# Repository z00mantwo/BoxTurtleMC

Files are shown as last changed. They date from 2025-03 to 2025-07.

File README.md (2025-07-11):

# BoxTurtleMC 
BoxTurtle Motor Controller. This is a self sourced DC motor controller for use with [Klipper](https://github.com/ArmoredTurtle/BoxTurtleg) and the  [BoxTurtle](https://klipper3d.org) project. This is not an official [Armored Turtle](https://github.com/ArmoredTurtle) project. Please read the entire file before ordering any parts so you know your options and what is involved. 

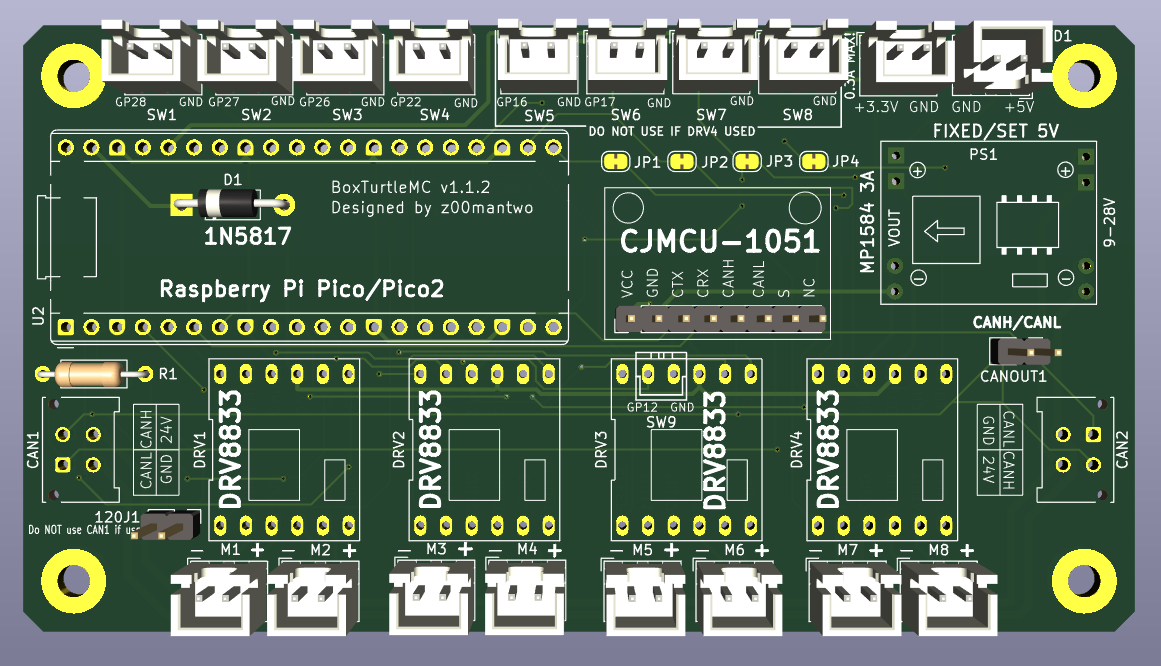
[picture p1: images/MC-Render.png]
BT_Render


The main focus is combining this project with a [BigTreeTech MMB](https://biqu.equipment/products/bigtreetech-mmb). This will enable full BoxTurtle control of the DC motor powered re-spoolers. It also allows a nice upgrade path from a ERCF to the BoxTurtle. It includes additional switch ports to support the "BoxTurtle Lane Controls" mod and additional power connections to support  [Project TurtleScreen](https://github.com/sbtoonz/TurtleScreen). This board will also have the option of controlling up to 8 re-spooler motors so it should be useful in larger custom BoxTurtle setups with more than 4 lanes. 

The board was developed in the free version of [KiCAD](https://www.kicad.org/). So it can be downloaded and modified.

Note there is a mount for the board in the stl folder.

## Making a PCB
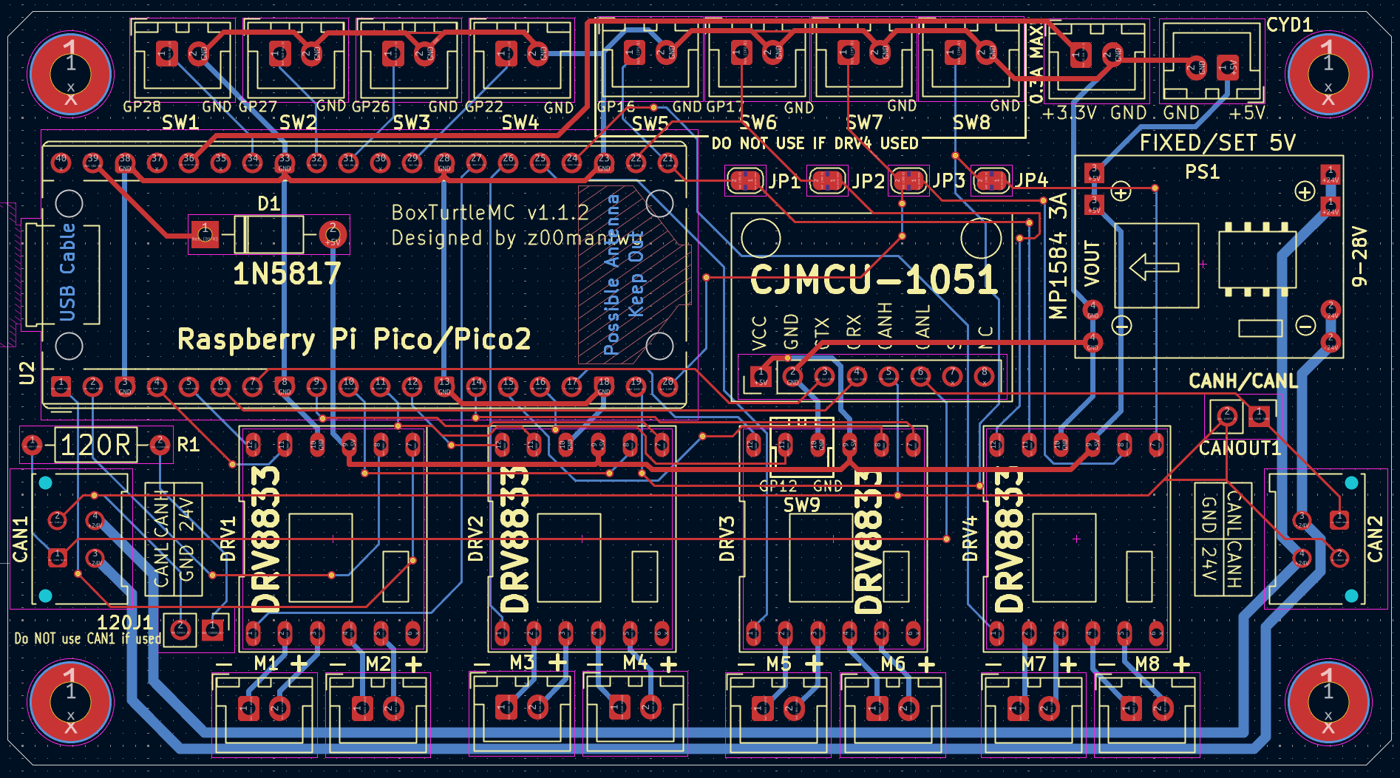
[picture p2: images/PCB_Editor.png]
 

Download the latest zip file from the gerber folder. This file can then be submitted to one of the PCB manufactures online like [PCBWay.com](https://www.pcbway.com/), [HQ NextPCB](https://www.nextpcb.com/), [ALLPCB](https://www.allpcb.com/) or [JLCPcb.com](https://jlcpcb.com/). Orders are usually a minimum of 5 PCBs per order and should be around $30 USD for 5 boards including shipping. If this is your first time doing this there are often "first time customer" discounts that can push the cost below $20 including shipping. I suggest shopping around to find the best deal. 

Ideally those who go through the process to make circuit boards will make their extra boards available to others at a minimum cost. The "[Garage Sale](https://discord.com/channels/1229586267671629945/1320411766290907238)" forum in the BoxTurtle Discord is a great place to do this. 

## BOM
All parts are available on Amazon with the exception of the 2 CANBUS plugs.
Those are available at [DigiKey.com](https://DigiKey.com).  

| Item | Quantity | Notes | Links |
| :--- | :---: |:--- | :--- |
PCB | 1 | Required. See "Making a PCB" section | 
Raspberry Pi Pico or Pico 2 | 1 | Required. "W"ireless version is not needed, but will work. | [Amazon](https://www.amazon.com/s?k=Raspberry+Pi+Pico)
1N5817 Diode | 1 | Required. |[Amazon](https://www.amazon.com/s?k=1N5817+Diode)
MP1583EN DC-DC buck converter | 1 | Required. 5V FIXED version highly suggested. Make sure to get version with 8 mounting holes. | BT_Render [Amazon](https://www.amazon.com/s?k=MP1583EN+dc-dc+5v+buck+converter)
CJMCU-1051 | 1 | Requied if using CANBUS. CANBUS is the suggested communications method. | [Amazon](https://www.amazon.com/s?k=CJMCU-1051)
DRV8833 DC Motor Driver | 2-4 | One required for each pair of motors. Make sure to get the 12pin 1.5A Dual H Bridge version. | [Amazon](https://www.amazon.com/s?k=DRV8833+DC+Motor+Driver+Controller+Board+3A+Dual+H+Bridge)
Molex Micro-Fit 3.0 43045 | 2 | CANBUS socket. Look at the bottom of the DigiKey page for "Mating Products" if you need the plugs. | [Digikey](https://www.digikey.com/en/products/detail/molex/0430450414/252509)
2.54mm 20 pin female header | 2 |  To socket Pi Pico/Pico 2 | [Amazon](https://www.amazon.com/s?k=2.54mm+Female+Pin+Header)
2.54mm 8 pin female pin header | 1 | For CJMCU-1051.  | [Amazon](https://www.amazon.com/s?k=2.54mm+Female+Pin+Header)
2.54mm 6 pin female pin header | 4 or more | 2 for each DRV8833 module.  | [Amazon](https://www.amazon.com/s?k=2.54mm+Female+Pin+Header)
JST XH 2.54mm 2-pin female sockets | 4 or more | This depends on what parts of the board you will make use of. | [Amazon](https://www.amazon.com/s?k=JST-XH+2.54mm+2pin+female+sockets) 
Through hole 120 Ohm axial resister | 1 | Only needed if CANBUS termination is needed. |  
2pin 2.54mm Pitch Single Row Pin Header | 1,2 | Used for jumper to turn on CANBUS termination. Another one is used for CANH/CANL connection. Both are optional. | [Amazon](https://www.amazon.com/s?k=2.54mm+Pitch+Single+Row+Pin+Header)

If you need to terminate this board use the CAN2 connector for the incoming CANBUS connection. Do not use the CAN1 connection when terminated. 

Note when ordering the Molex Micro-Fit 3.0 connector headers you may also want to order some [Molex Micro-Fit 3.0 plugs](https://www.digikey.com/en/products/detail/molex/0430250408/4481508) along with the appropriate pins [Molex 0430300007](https://www.digikey.com/en/products/detail/molex/0430300007/252479). Since DigiKey allows ordering in specified quantities as low as 1 this may also be a good place to source the needed diode and optional resister.

## Tools Needed
- Basic experience soldering components.
- Soldering iron with fine tip.
- Good solder. Thinner is better.

## Assembling PCB
Solder on the 2 CANBUS plugs and the MP1583EN module. It is recommended that the MP1583EN be soldered to the board and not socketed. If you didn't get a fixed 5V MP1583EN then make sure to set it to 5V. You can do this by connecting the board to a CANBUS connection and adjusting the potentiometer on the MP1583EN while monitoring the output voltage via the 5V connector with a multi meter. Note a fixed 5V MP1583EN is suggested to bypass this step and avoid issues.

Solder in the 1N5817 diode. Note if you are soldering the Pico to the board (not recommended) the diode will need to be installed on the back of the circuit board.

Next solder on the socket connectors as needed. It is recommended to socket the Pico and the DRV8833 modules. The DRV8833 modules are sensitive to static shock. So this makes them easy to replace if needed. 

Solder in the optional CANBUS terminator resister and pin header if needed.

## CANBUS: Flashing Katapult and Klipper

CANBUS needs to already be setup and working on your printer. [Esoterical’s guide](https://canbus.esoterical.online/) is a great resource.

First step is to put Katapult on the Pi Pico. If Katapult isn't already on your Klipper host follow the instructions from the Katapult website to install it on your Klipper host. Instructions are available at [https://github.com/Arksine/katapult](https://github.com/Arksine/katapult). 

Configure katapult as shown below.

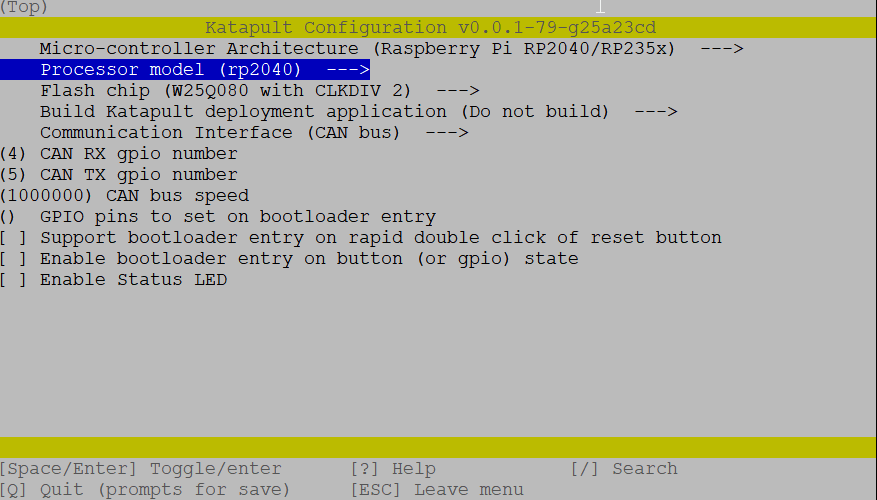
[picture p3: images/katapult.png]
 

Note if you are using a Pi Pico 2 change the "Processor Model" to rp2350.

After configuring and making katapult. Connect your Pi Pico while pressing the boot button on the Pico via USB to your klipper host. It is suggested the Pico is not in the BoxTurtleMC board at this point. 

Then at the hosts command line type lsusb. The Pico should be listed as "Raspberry Pi RP2040 Boot" or "Raspberry Pi RP2350 Boot" if it's a Pico 2. Make a note of the Pico's address. It should be something like "2e8a:000f" as shown below. 

```
~/katapult $ lsusb
Bus 002 Device 002: ID 2109:0817 VIA Labs, Inc. USB3.0 Hub
Bus 002 Device 001: ID 1d6b:0003 Linux Foundation 3.0 root hub
Bus 001 Device 007: ID 0eef:0005 D-WAV Scientific Co., Ltd WS170120
Bus 001 Device 009: ID 1d50:614e OpenMoko, Inc. rp2040
Bus 001 Device 012: ID 2e8a:000f Raspberry Pi RP2350 Boot
Bus 001 Device 006: ID 1d50:606f OpenMoko, Inc. Geschwister Schneider CAN adapter
Bus 001 Device 002: ID 2109:3431 VIA Labs, Inc. Hub
Bus 001 Device 001: ID 1d6b:0002 Linux Foundation 2.0 root hub
```

Now flash the Pico using the following command `sudo make flash device=2e8a:000f` substituting the address of your Pico while in the katapult directory. You should see several messages like below after flashing is complete.

```
~/katapult $ sudo make flash device=2e8a:000f
Flashing out/katapult.uf2
Loaded UF2 image with 29 pages
Found rp2040 device on USB bus 1 address 11
Flashing...
Resetting interface
Locking
Exiting XIP mode
Erasing
Flashing
Rebooting device
```

Put you Pico in the BoxTurtleMC board and connect the board to your CANBUS cable. Make sure to power everything off before doing that and then bring everything back up.

Check if the Pico is detected on the CANBUS with the command `~/klipper/scripts/canbus_query.py can0`. Output should look something like:

```
~/klipper $ ~/klippy-env/bin/python ~/klipper/scripts/canbus_query.py can0
Found canbus_uuid=05a32df28477, Application: Klipper
Total 1 uuids found
```

If the Pico isn't found then something went wrong in the process of flashing or something is wrong with your CANBUS cabling or setup.

Record the UUID given for the Pico. You will need this to flash klipper and to configure klipper.

Reconnect to the command line on your klipper host. Next change to the klipper directory. There run the command `make menuconfig` and change the settings as shown below.

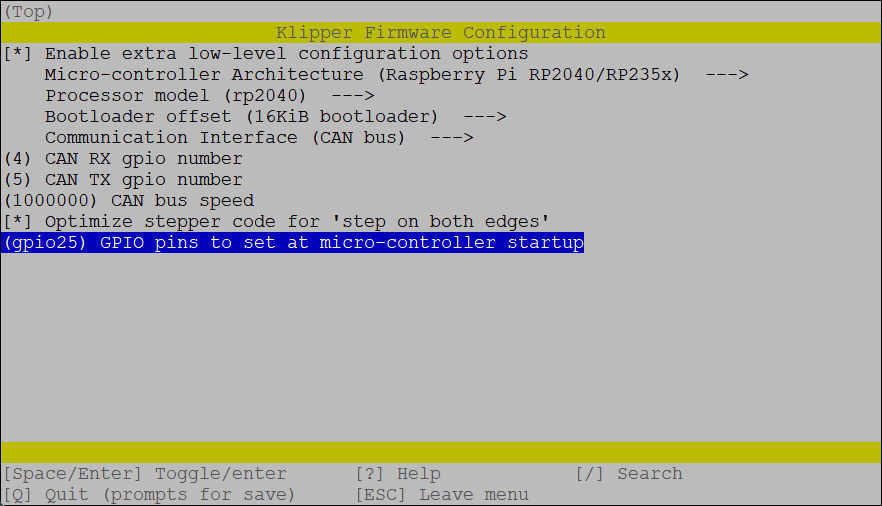
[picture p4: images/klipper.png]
 

Note if you are using a Pi Pico 2 change the "Processor Model" to rp2350.

Make klipper then flash it to the Pico with the command below. Substitute the uuid (XXXXXXXXXXXX) with your Pico's uuid you recorded above.

```
cd ~/katapult/scripts && python3 flashtool.py -i can0 -f ~/klipper/out/klipper.bin -u XXXXXXXXXXXX
```

If all is well the Pico will reboot and there should be a green light on the Pi Pico and a red light on each DRV8833. If the Pico light does not come on power off and back on. If it still does not come on something went wrong along the way. 

## Klipper configuration

Copy the `MC_1.cfg` in the klipper folder to your klipper configurations folder. 

Then add

```
[include MC_1.cfg]
```

to your `printer.cfg`. Make sure this is before you load the [AFC-Klipper-Add-On](https://github.com/ArmoredTurtle/AFC-Klipper-Add-On/tree/main) cfg files. 

Note that with the DRV8833 modules use one line controls the SLEEP/ENABLE option for 2 motors. So rather than a MOT1_EN alias the BoxTurtleMC has a MOT12_EN alias that is the ENABLE function for both motor 1 and motor 2.

This then requires setting a `[duplicate_pin_override]` section in your klipper configuration. See the example near the end of the `MC_1.cfg` file for an example. Note that if you don't have a `[duplicate_pin_override]` section in your current configuration you can uncomment the section in the `MC_1.cfg` file.

If you are combining the BoxTurtleMC with BTT MMB you will need to edit the AFC/mcu/MMB_1.0.cfg or MMB_1.1.cfg and remove or comment out the MOT lines by placing a # in front of each line.

```
	#MOT1_RWD=PA0	, 
	#MOT2_RWD=PA1	, 
	#MOT3_RWD=PB10	, 
	#MOT4_RWD=PB2	,
```

Then you need to change the "afc_motor" entries in your `AFC/AFC_Turtle_1.cfg` file for each lane that you want the re-spooler motors controlled by the BoxTurtleMC. For example change

```
afc_motor_rwd: Turtle_1:MOT1_RWD
afc_motor_fwd: Turtle_1:MOT1_FWD
afc_motor_enb: Turtle_1:MOT1_EN
```

to

```
afc_motor_rwd: MC_1:MOT1_RWD
afc_motor_fwd: MC_1:MOT1_FWD
afc_motor_enb: MC_1:MOT12_EN
```

You will need to do this for each lane that you want the BoxTurtleMC to control the DC motor in the re-spooler. 

Use the [AFC Klipper Add-on](https://github.com/ArmoredTurtle/AFC-Klipper-Add-On/)'s "TEST lane=lane1" to check each motor control is setup properly. 

## Options
- You can use a JST XH 2.54mm 2-pin female socket for the CANH/CANL rather than a 2 pin header if you want.
 
- Only purchasing the components you need. All locations on the board do not need to be populated. You can choose and select the ones you want to populate based on your intended usage. Below is a board setup to only use motors 1-4.

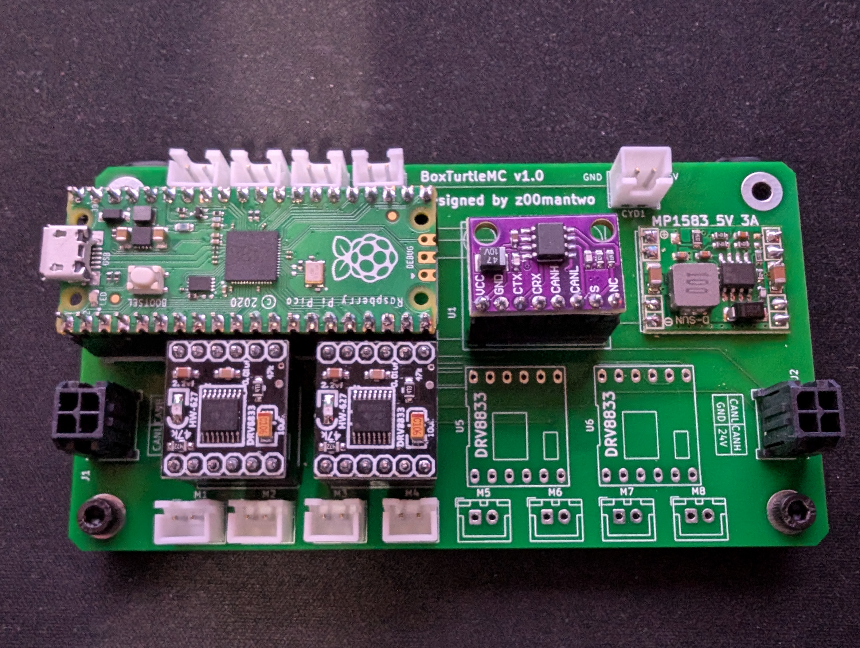
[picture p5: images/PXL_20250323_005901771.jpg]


- A question was asked about using this board with a cheap Ender 3 SKR board. Most of the SKR boards only have 4 switches. X, Y, Z limit switches and a filament detection switch. When combined with this board's 6 switches that would only be 10 switches and 11 are needed for a 4 lane BoxTurtle. The DRV3 socket can be used to add a 7th switch as shown below. Make sure to orient the socket as shown. This would make the 7th switch GPIO12. NOTE THIS HAS NOT BEEN TESTED, but should work.

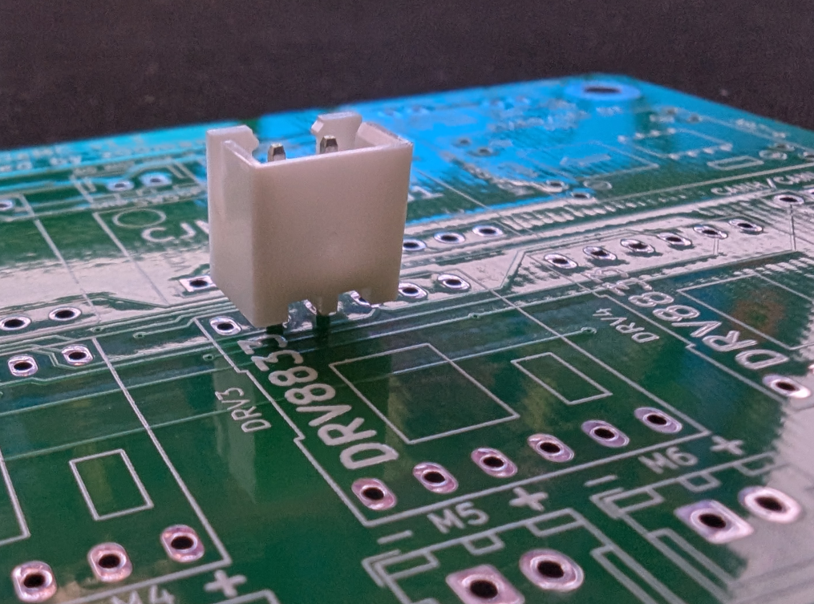
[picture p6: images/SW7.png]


- Using USB rather than CANBUS. This board can be used by klipper through the USB connector on the Pi Pico. The CJMCU-1051 could then be excluded, but the board would still need external 24V power for the DRV8833s. This can be connected via one of the CANBUS connectors. This will require install klipper (no katapult) as configured below. Only recommended for experienced klipper users. 

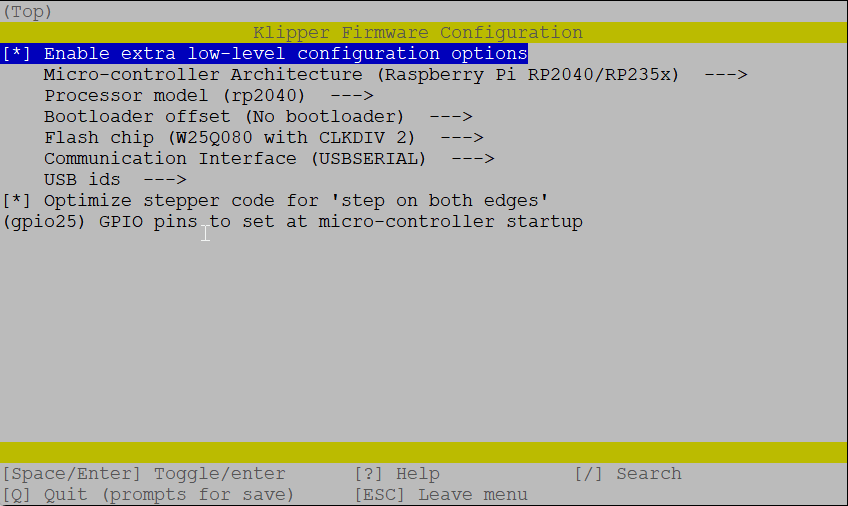
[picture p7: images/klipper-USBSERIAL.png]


Note if you are using a Pi Pico 2 change the "Processor Model" to rp2350.

## Version 1.1.2 boards (Current Release)
This is a minor upgrade over 1.1 boards. It added 2 additional switches when DRV4 is not populated and an additional 9th switch when DRV3 is also not populated. This is primarily to support using this board with MCUs that have a limited number of switch connections. To get to the required 11 switches needed for a base model, 4 lane, BoxTurtle.

## Version 1.1 boards
Release 1.1 boards only included 6 switches. Two of which only worked if DRV4 is left empty. This was the first version released. 

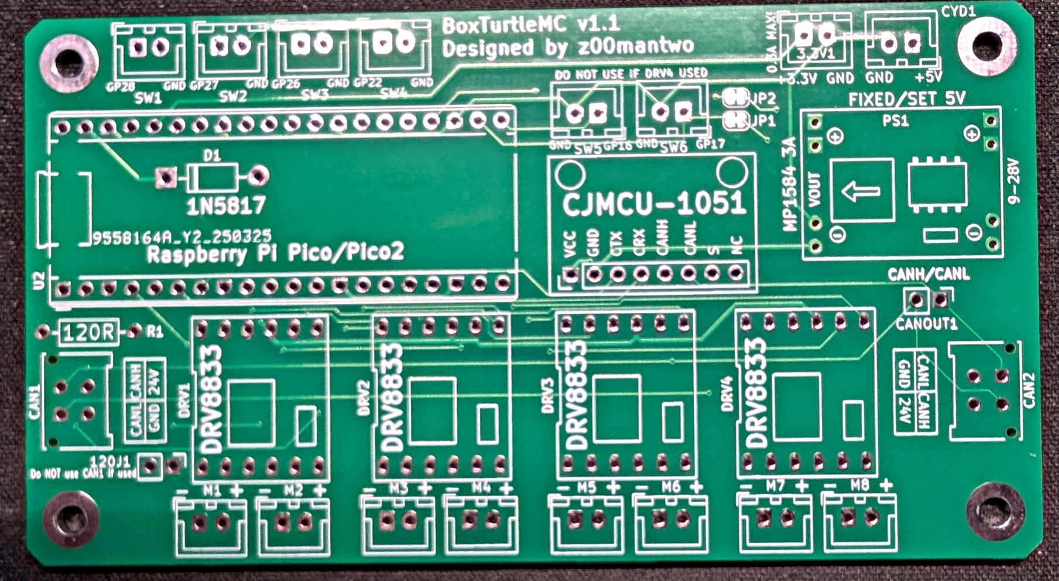
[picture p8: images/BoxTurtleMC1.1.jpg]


## Early release 1.0 boards
Note the 1.0 board does have a known issue. The CANL and CANH pins are reversed. Still works, but where katapult and klipper want to use pins 4 and 5 as defaults you have to switch them to 5 then 4. Version 1.1 board fixes this. See the screenshots in the "Flashing Katapult and Klipper" section above.

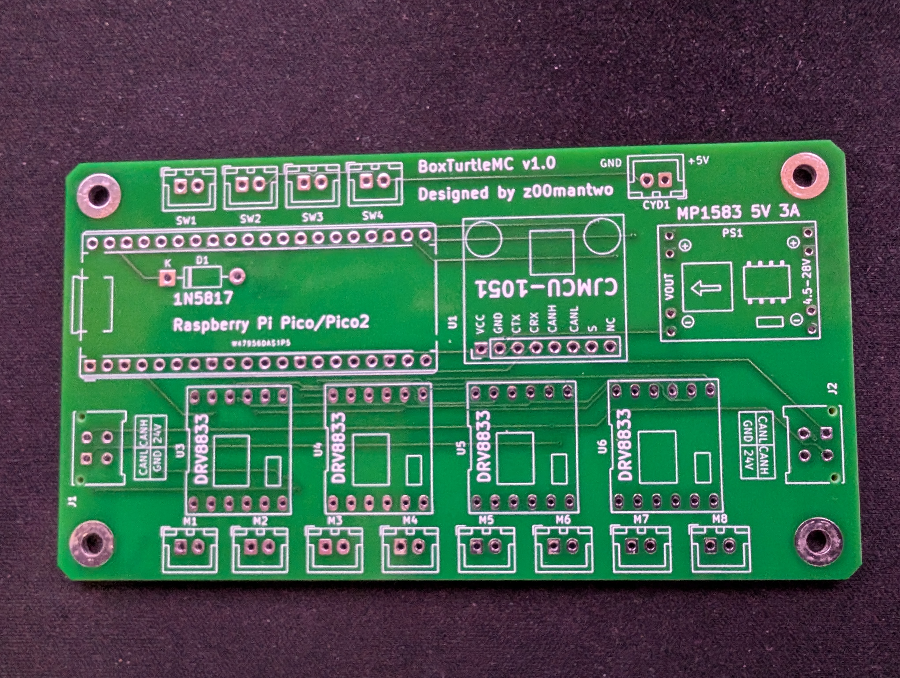
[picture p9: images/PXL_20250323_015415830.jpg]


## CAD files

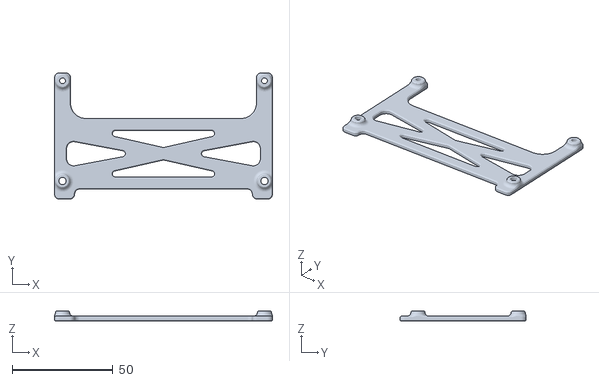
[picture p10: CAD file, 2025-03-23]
stl/MC_Mount.stl
108.0 x 62.6 x 5.00

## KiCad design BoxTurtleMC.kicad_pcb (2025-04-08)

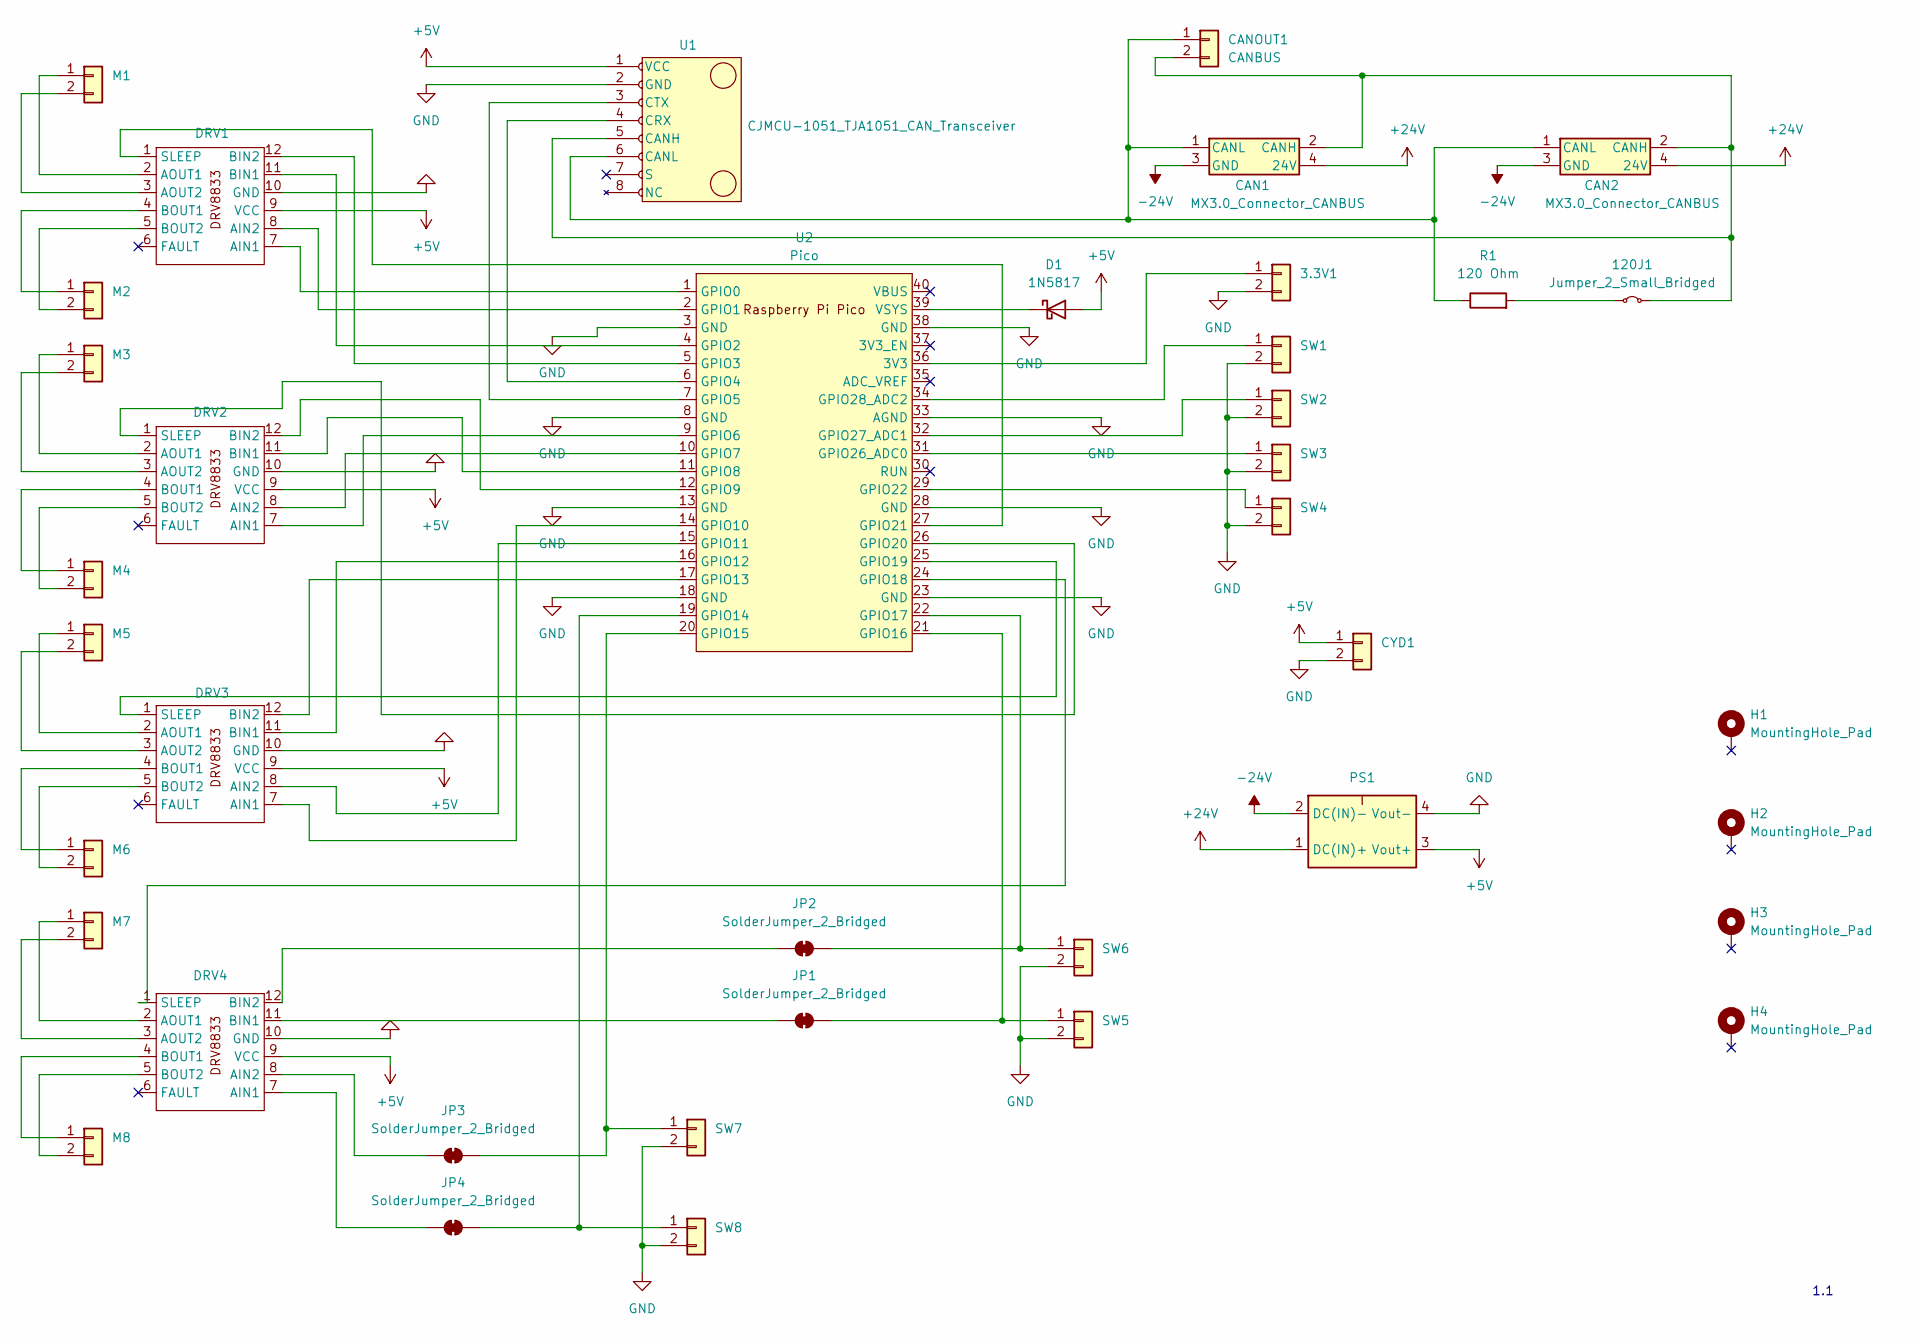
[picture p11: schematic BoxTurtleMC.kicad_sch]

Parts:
3.3V1: 1; JST_XH_B2B-XH-A_1x02_P2.50mm_Vertical
120J1: Jumper_2_Small_Bridged; PinHeader_1x02_P2.54mm_Vertical
CAN1, CAN2: MX3.0_Connector_CANBUS; MX3.0 Connector CANBUS
CANOUT1: CANBUS; PinHeader_1x02_P2.54mm_Vertical
CYD1: 1; JST_XH_B2B-XH-A_1x02_P2.50mm_Vertical
D1: 1N5817; D_DO-41_SOD81_P10.16mm_Horizontal
DRV1, DRV2, DRV3, DRV4: DRV8833_Module
H1, H2, H3, H4: MountingHole_Pad; MountingHole_3.2mm_M3_Pad_TopBottom
JP1, JP2, JP3, JP4: SolderJumper_2_Bridged; SolderJumper-2_P1.3mm_Bridged_RoundedPad1.0x1.5mm
M1, M2, M3, M4, M5, M6, M7, M8: Conn_01x02 Pin1+ Pin2-; JST_XH_B2B-XH-A_1x02_P2.50mm_Vertical
PS1: MP1583_Module; MP1584_Module
R1: 120 Ohm; R_Axial_DIN0207_L6.3mm_D2.5mm_P10.16mm_Horizontal
SW1, SW2, SW3, SW4, SW5, SW6, SW7, SW8: Conn_01x02 Pin1+ Pin2-; JST_XH_B2B-XH-A_1x02_P2.50mm_Vertical
U1: CJMCU-1051_TJA1051_CAN_Transceiver
U2: Pico; RaspberryPi_Pico_Common_THT

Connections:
+5V: CYD1.1, D1.2 (A), DRV1.9 (VCC), DRV2.9 (VCC), DRV3.9 (VCC), DRV4.9 (VCC), PS1.3 (Vout+), U1.1 (VCC)
+24V: CAN1.4 (24V), CAN2.4 (24V), PS1.1 (DC(IN)+)
-24V: CAN1.3 (GND), CAN2.3 (GND), PS1.2 (DC(IN)-)
GND: 3.3V1.2, CYD1.2, DRV1.10 (GND), DRV2.10 (GND), DRV3.10 (GND), DRV4.10 (GND), PS1.4 (Vout-), SW1.2, SW2.2, SW3.2, SW4.2, SW5.2, SW6.2, SW7.2, SW8.2, U1.2 (GND), U2.3 (GND), U2.8 (GND), U2.13 (GND), U2.18 (GND), U2.23 (GND), U2.28 (GND), U2.33 (AGND), U2.38 (GND)
unnamed: 3.3V1.1, U2.36 (3V3)
unnamed: 120J1.1 (A), R1.2
unnamed: 120J1.2 (B), CAN1.2 (CANH), CAN2.2 (CANH), CANOUT1.2, U1.5 (CANH)
unnamed: CAN1.1 (CANL), CAN2.1 (CANL), CANOUT1.1, R1.1, U1.6 (CANL)
unnamed: D1.1 (K), U2.39 (VSYS)
unnamed: DRV1.7 (AIN1), U2.1 (GPIO0)
unnamed: DRV1.8 (AIN2), U2.2 (GPIO1)
unnamed: DRV1.2 (AOUT1), M1.1
unnamed: DRV1.3 (AOUT2), M1.2
unnamed: DRV1.11 (BIN1), U2.4 (GPIO2)
unnamed: DRV1.12 (BIN2), U2.5 (GPIO3)
unnamed: DRV1.4 (BOUT1), M2.1
unnamed: DRV1.5 (BOUT2), M2.2
unnamed: DRV1.1 (SLEEP), U2.27 (GPIO21)
unnamed: DRV2.7 (AIN1), U2.9 (GPIO6)
unnamed: DRV2.8 (AIN2), U2.10 (GPIO7)
unnamed: DRV2.2 (AOUT1), M3.1
unnamed: DRV2.3 (AOUT2), M3.2
unnamed: DRV2.11 (BIN1), U2.11 (GPIO8)
unnamed: DRV2.12 (BIN2), U2.12 (GPIO9)
unnamed: DRV2.4 (BOUT1), M4.1
unnamed: DRV2.5 (BOUT2), M4.2
unnamed: DRV2.1 (SLEEP), U2.26 (GPIO20)
unnamed: DRV3.7 (AIN1), U2.14 (GPIO10)
unnamed: DRV3.8 (AIN2), U2.15 (GPIO11)
unnamed: DRV3.2 (AOUT1), M5.1
unnamed: DRV3.3 (AOUT2), M5.2
unnamed: DRV3.11 (BIN1), U2.16 (GPIO12)
unnamed: DRV3.12 (BIN2), U2.17 (GPIO13)
unnamed: DRV3.4 (BOUT1), M6.1
unnamed: DRV3.5 (BOUT2), M6.2
unnamed: DRV3.1 (SLEEP), U2.25 (GPIO19)
unnamed: DRV4.7 (AIN1), JP4.1 (A)
unnamed: DRV4.8 (AIN2), JP3.1 (A)
unnamed: DRV4.2 (AOUT1), M7.1
unnamed: DRV4.3 (AOUT2), M7.2
unnamed: DRV4.11 (BIN1), JP1.1 (A)
unnamed: DRV4.12 (BIN2), JP2.1 (A)
unnamed: DRV4.4 (BOUT1), M8.1
unnamed: DRV4.5 (BOUT2), M8.2
unnamed: DRV4.1 (SLEEP), U2.24 (GPIO18)
unnamed: JP1.2 (B), SW5.1, U2.21 (GPIO16)
unnamed: JP2.2 (B), SW6.1, U2.22 (GPIO17)
unnamed: JP3.2 (B), SW7.1, U2.20 (GPIO15)
unnamed: JP4.2 (B), SW8.1, U2.19 (GPIO14)
unnamed: SW1.1, U2.34 (GPIO28_ADC2)
unnamed: SW2.1, U2.32 (GPIO27_ADC1)
unnamed: SW3.1, U2.31 (GPIO26_ADC0)
unnamed: SW4.1, U2.29 (GPIO22)
unnamed: U1.4 (CRX), U2.6 (GPIO4)
unnamed: U1.3 (CTX), U2.7 (GPIO5)

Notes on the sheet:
1.1

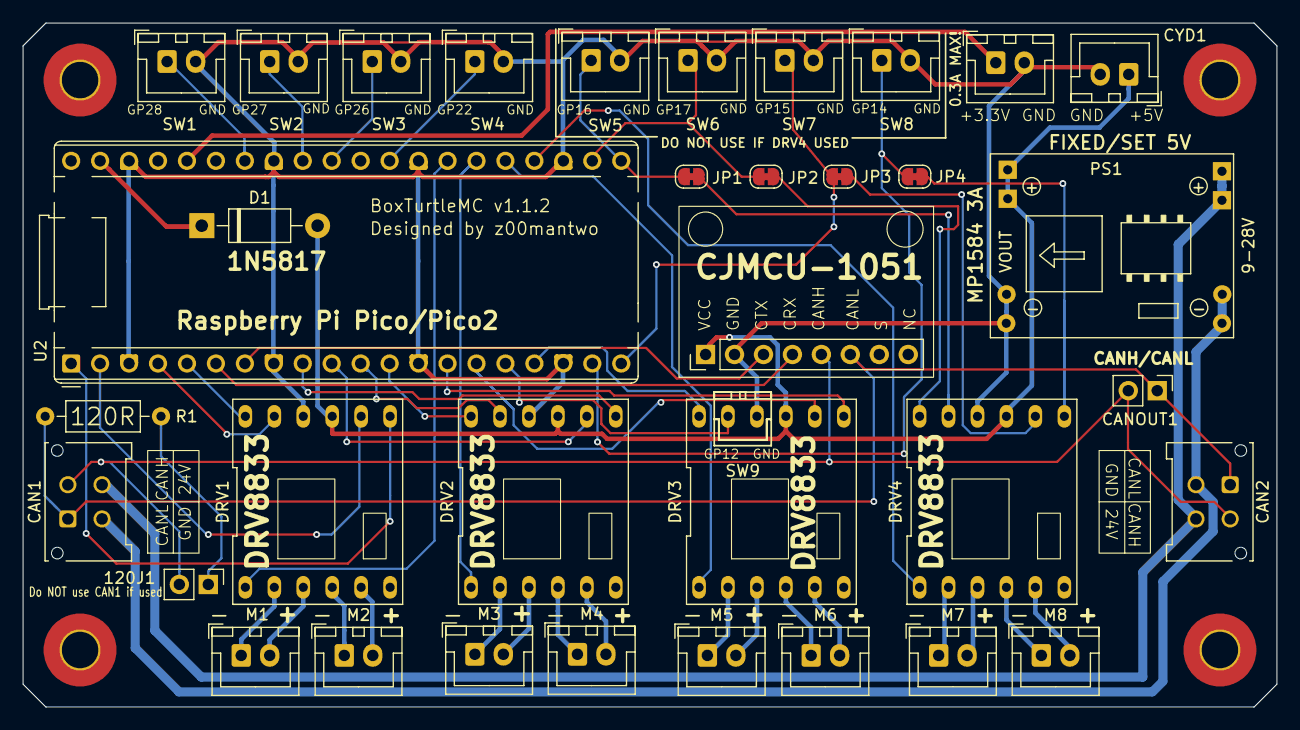
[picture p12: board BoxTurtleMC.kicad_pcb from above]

Board: 2 copper layers, 110.0 x 60.0 mm, 39 parts (0 on the bottom side), 55 nets.

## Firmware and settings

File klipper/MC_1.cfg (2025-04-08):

[mcu MC_1]
#
#canbus_uuid: <can UID>
# Pi Pico/Pico2 via CANBUS
#canbus_uuid: e68d4f167761
# 
# USB(SERIAL) Connection via Pico/Pico2 USB port
#serial: /dev/serial/by-id/usb-Klipper_rp2040_E66038B7134F192F-if00
#restart_method: command

# Add temp of MC baord's Pi Pico
[temperature_sensor MC_1]
sensor_type: temperature_mcu
sensor_mcu: MC_1

[board_pins MC_1]
mcu: MC_1
aliases:
# Switches for Lane Control buttons
    SW1=gpio28,		 SW2=gpio27 		, SW3=gpio26  		, SW4=gpio22, 
	# If DRV4 is NOT populated two additional switches are available. SW5 and SW6. 
	# ONLY uncomment the line below if DRV4 is NOT installed on the board. 
	# SW5=gpio16,	 SW6=gpio17, 
	# If DRV3 is NOT populated one additional switche is available. SW7. 
	# ONLY uncomment the line below if DRV3 is NOT installed on the board. 
	# You will also need to comment out MOT6_FWD in the Motor driver pins section. 
	# SW7=gpio12, 
	
# Motor driver pins
    MOT1_RWD=gpio1	, MOT1_FWD=gpio0	, 
    MOT2_RWD=gpio3	, MOT2_FWD=gpio2	, 
    MOT3_RWD=gpio7	, MOT3_FWD=gpio6	, 
    MOT4_RWD=gpio9	, MOT4_FWD=gpio8	, 
    MOT5_RWD=gpio11	, MOT5_FWD=gpio10	, 
    MOT6_RWD=gpio13	, MOT6_FWD=gpio12	, 
    MOT7_RWD=gpio15	, MOT7_FWD=gpio14	, 
    MOT8_RWD=gpio17	, MOT8_FWD=gpio16	, 
    MOT12_EN=gpio21	,
    MOT34_EN=gpio20	,
    MOT56_EN=gpio19	,
    MOT78_EN=gpio18	

# Some pins are used mutiple times. 
# To prevent klipper complaining about this uncomment the section below
# or add these pins to an existing "[duplicate_pin_override]" in your klipper configs.
#[duplicate_pin_override]
#pins: MC_1:MOT12_EN,MC_1:MOT34_EN,MC_1:MOT56_EN,MC_1:MOT78_EN

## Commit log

2025-03-23 First update test
    [BoxTurtleMC1.kicad_pcb, BoxTurtleMC1.kicad_sch]
2025-03-23 Additional updates
    [BoxTurtleMC1.kicad_pcb_bom.csv, BoxTurtleMC1.kicad_pcb_positions.csv]
2025-04-03 Fix pin miss coding for motor 7 8
    [MC_1.cfg]
2025-04-03 Fixed some labels in schematic
    [BoxTurtleMC.kicad_sch]
2025-04-07 Added notes about using with Ender 3 SKR board.
    [BoxTurtleMC.kicad_pcb]
2025-04-07 Added notes about using with Ender 3 SKR board with pic
2025-04-07 Updated klipper config for SW5, SW6 and SW7.
    [MC_1.cfg]
2025-04-08 Added setup for USB connection
    [MC_1.cfg]
2025-04-08 Update to version 1.1.2
    [BoxTurtleMC.kicad_pcb, BoxTurtleMC.kicad_sch, MC_1.cfg]
